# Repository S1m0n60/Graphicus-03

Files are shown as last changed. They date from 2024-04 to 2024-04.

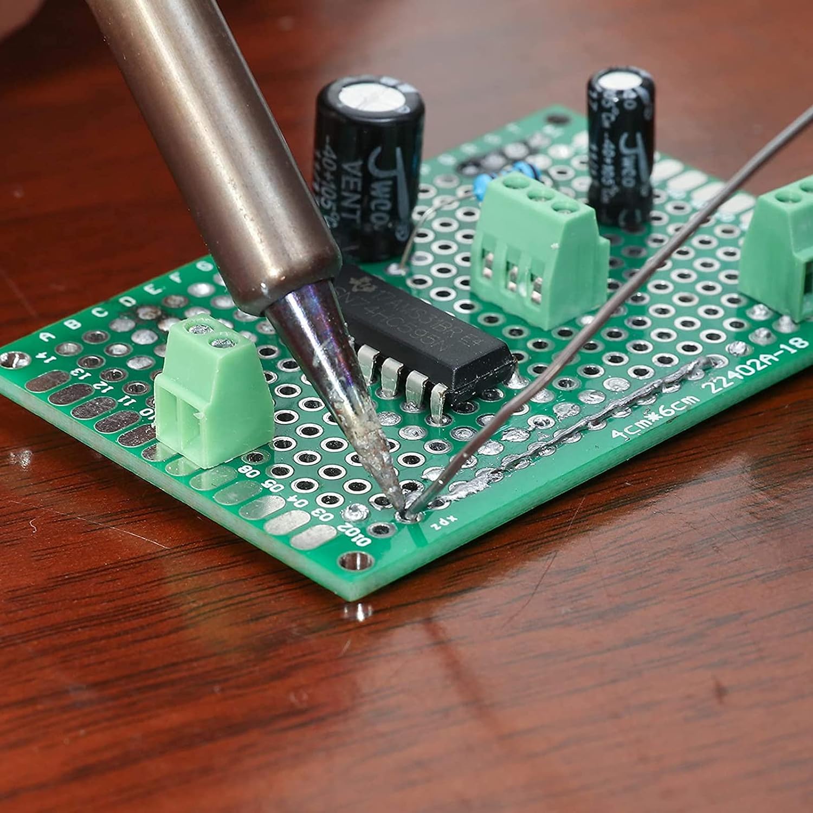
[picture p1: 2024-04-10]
Electrique/protoboard.jpg

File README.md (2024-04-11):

# **Graphicus-03**
## **Présentation**
<p style='text-align: justify;'> Graphicus-03 est une machine qui permet à l'opérateur de graver une image au choix sur un verre.
Ce repertoire permet à un utilisateur avec des connaissances de base en électronique, mécanique et informatique de fabriquer et mettre en marche un exemplaire de ce projet.
 
Pour plus d'informations, la documentation principale se trouve dans l' onglet [Wiki](https://github.com/S1m0n60/Graphicus-03/wiki) du projet.</p>

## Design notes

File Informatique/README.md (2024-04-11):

# **Section informatique**
<p style='text-align: justify;'>

Cette section contient toutes les ressources nécessaire pour faire l'intégration informatique de Graphicus-03.

Noter que les étapes à suivre pour effectuer l'assemblage se trouve dans le [Wiki](https://github.com/S1m0n60/Graphicus-03/wiki/Informatique).

</p>

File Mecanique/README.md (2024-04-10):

# **Section mécanique**
<p style='text-align: justify;'>

Cette section contient toutes les ressources nécessaire pour pouvoir assembler Graphicus-03.

Les ressources de cette section du répertoire sont divisé en deux section:

* [Les pièces à imprimer](https://github.com/S1m0n60/Graphicus-03/tree/main/Mecanique/Impression3D)
* [Les plan & devis](https://github.com/S1m0n60/Graphicus-03/tree/main/Mecanique/Plan%26Devis)

Noter que les étapes à suivre pour effectuer l'assemblage se trouve dans le [Wiki](https://github.com/S1m0n60/Graphicus-03/wiki/M%C3%A9canique).

</p>

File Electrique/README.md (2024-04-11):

# **Section électrique**
<p style='text-align: justify;'>

Cette section contient toutes les ressources nécessaire pour pouvoir réaliser les branchements de Graphicus-03.

## **Ressources importante**

* [Projet Autocad](https://github.com/S1m0n60/Graphicus-03/tree/main/Electrique/Team%20L%C3%A9vis%20et%20co)
* [Plan électrique en format PDF](https://github.com/S1m0n60/Graphicus-03/blob/main/Electrique/Team%20L%C3%A9vis%20et%20co.pdf)

Noter que les étapes à suivre pour effectuer l'assemblage se trouve dans le [Wiki](https://github.com/S1m0n60/Graphicus-03/wiki/%C3%89lectrique).

</p>

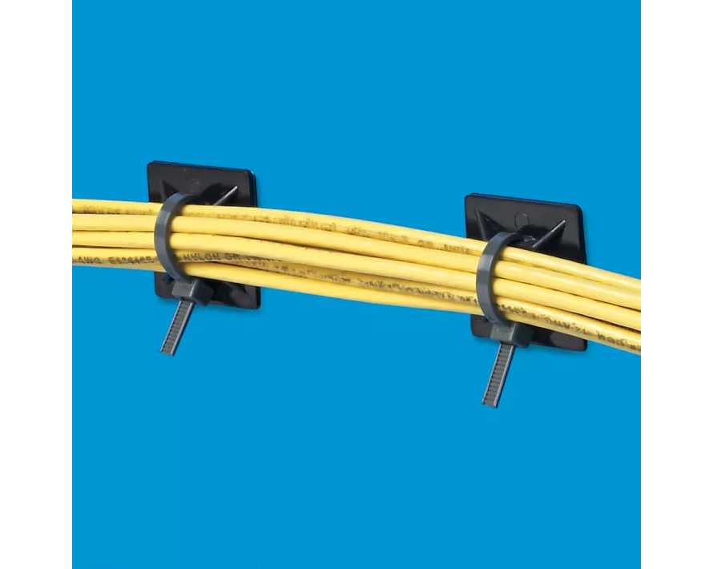
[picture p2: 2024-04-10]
Electrique/ZipTieCollant.png

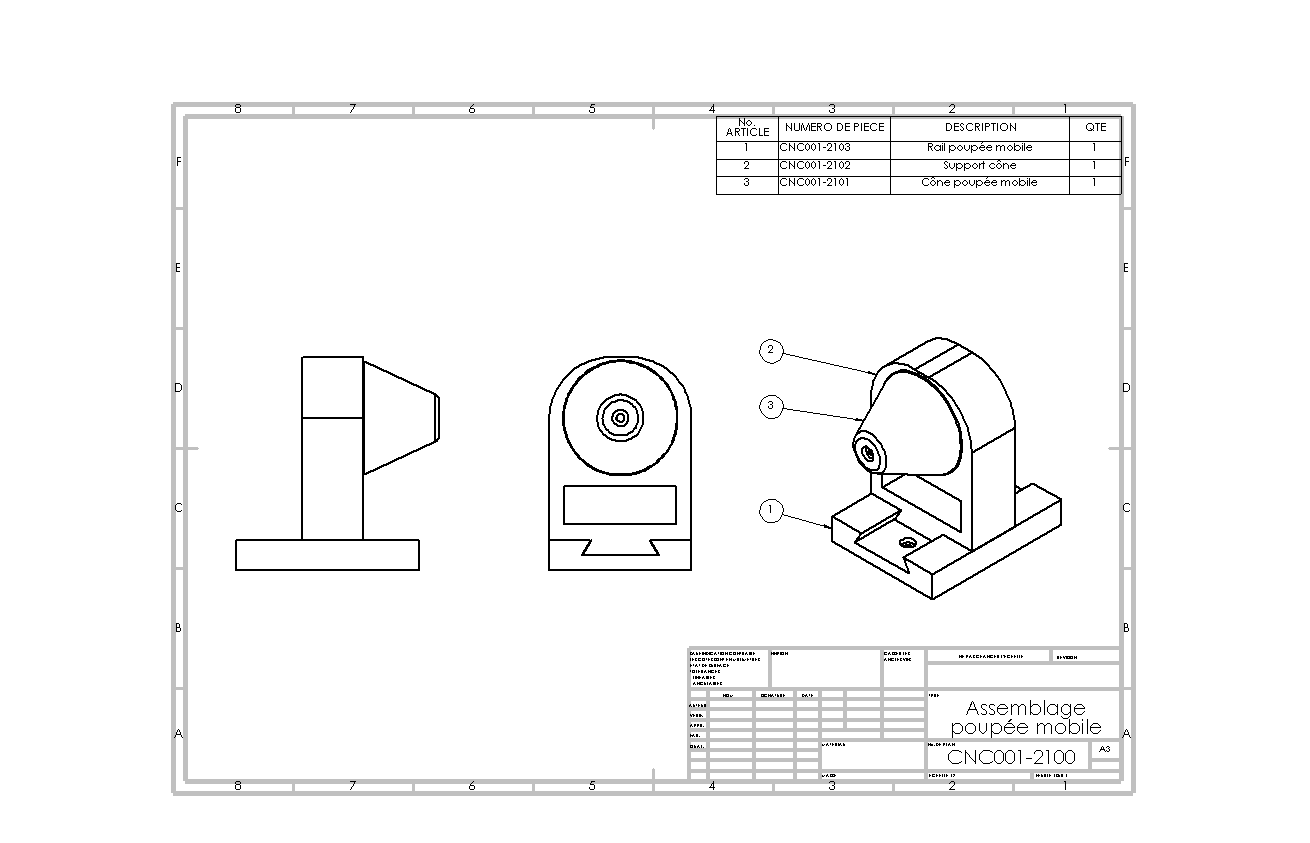
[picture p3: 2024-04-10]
Mecanique/Plan&Devis/Fichier_PNG/CNC001-2100.PNG

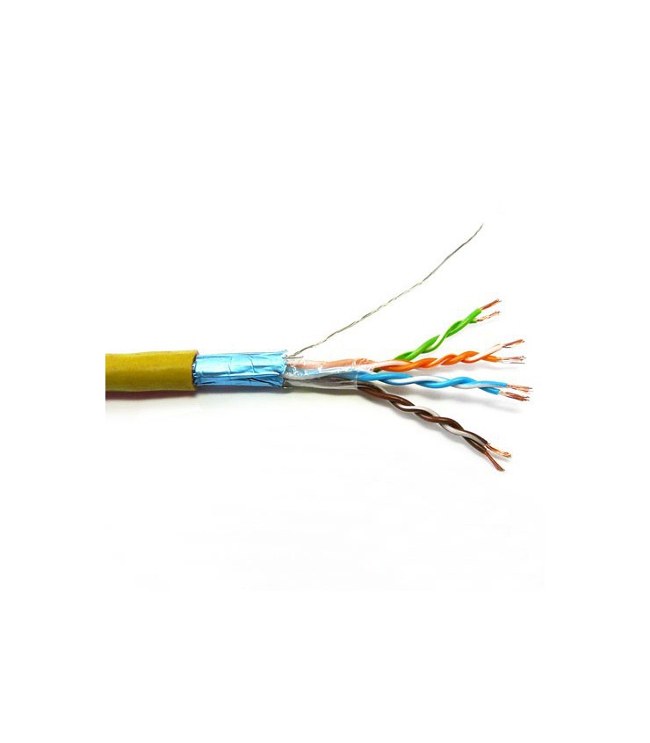
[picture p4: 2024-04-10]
Electrique/multibrin.jpg

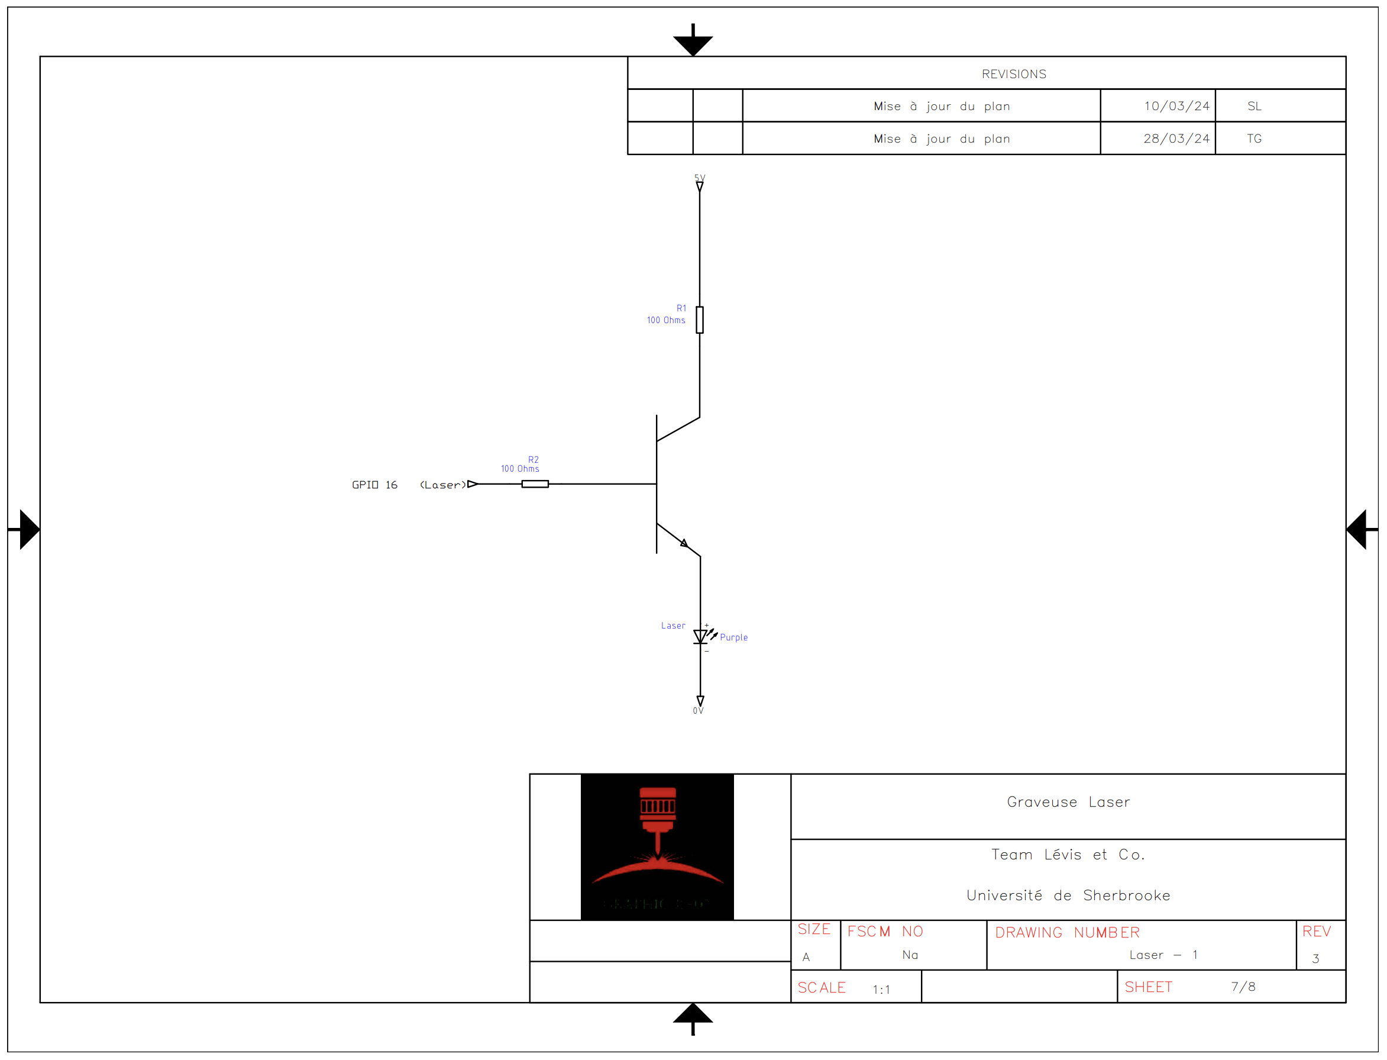
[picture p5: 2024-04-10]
Electrique/laser.PNG

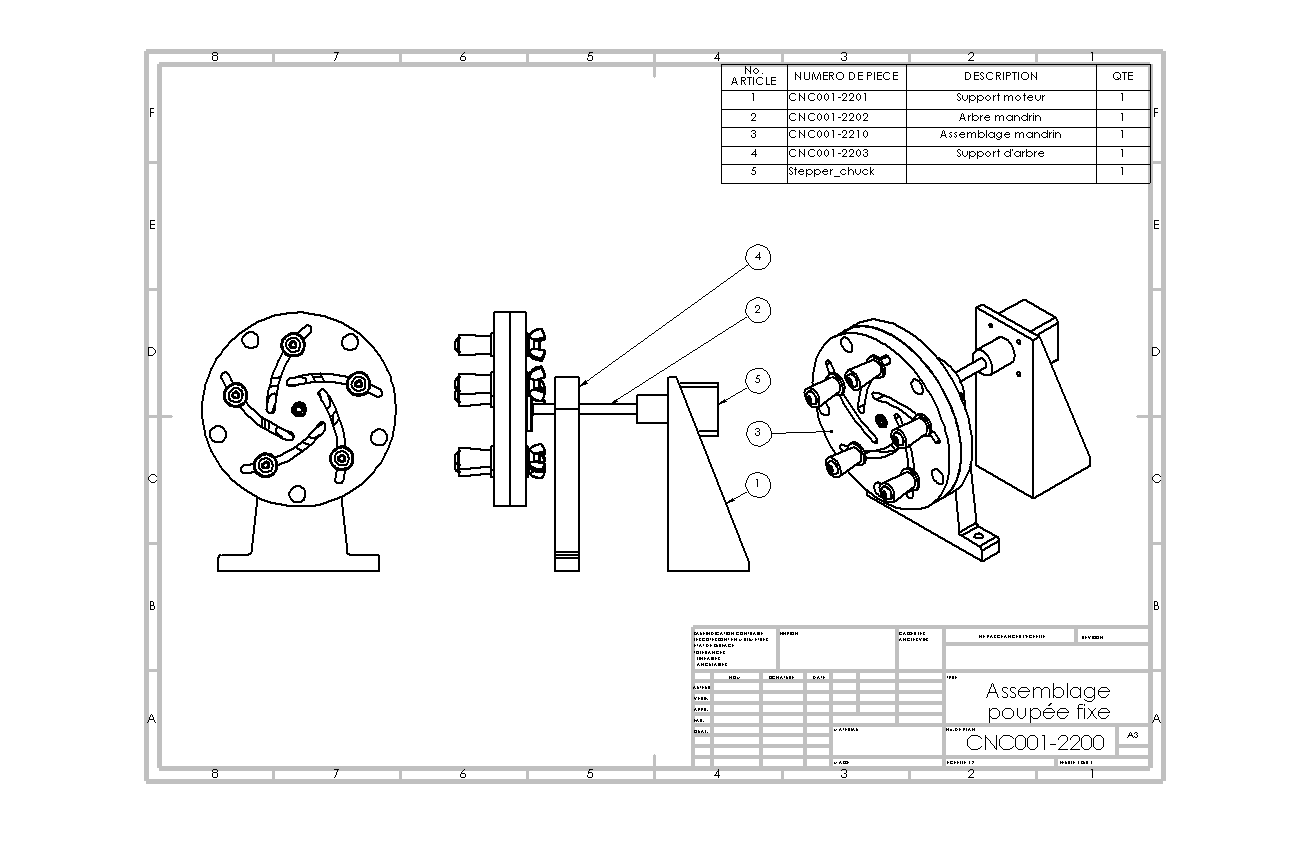
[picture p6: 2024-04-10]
Mecanique/Plan&Devis/Fichier_PNG/CNC001-2200.PNG

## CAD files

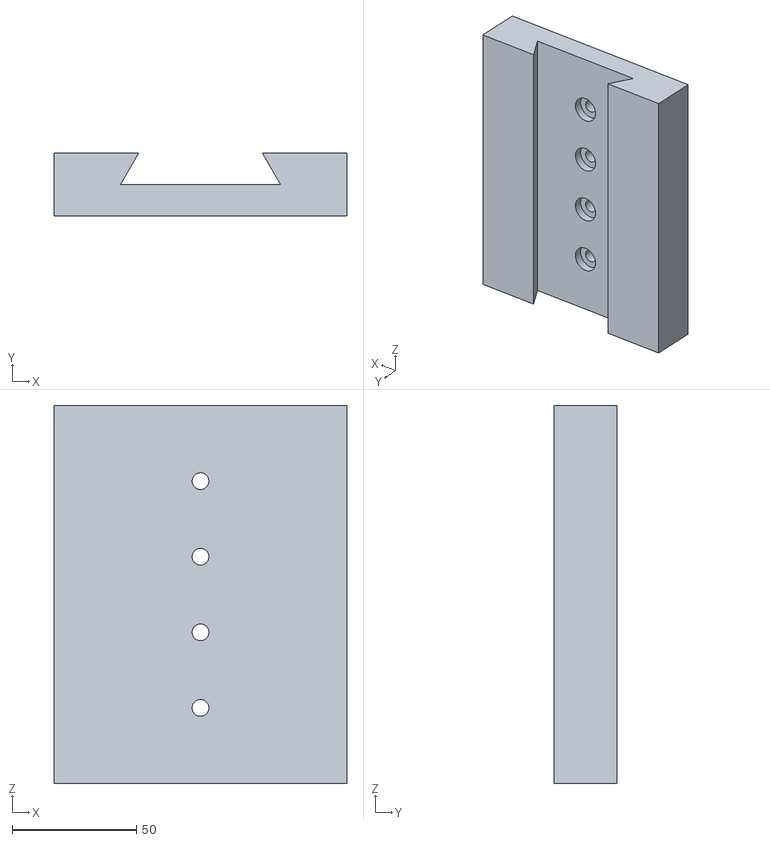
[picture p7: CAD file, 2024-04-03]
Mecanique/Impression3D/CNC001-2103.STL
118.1 x 25.4 x 152.4

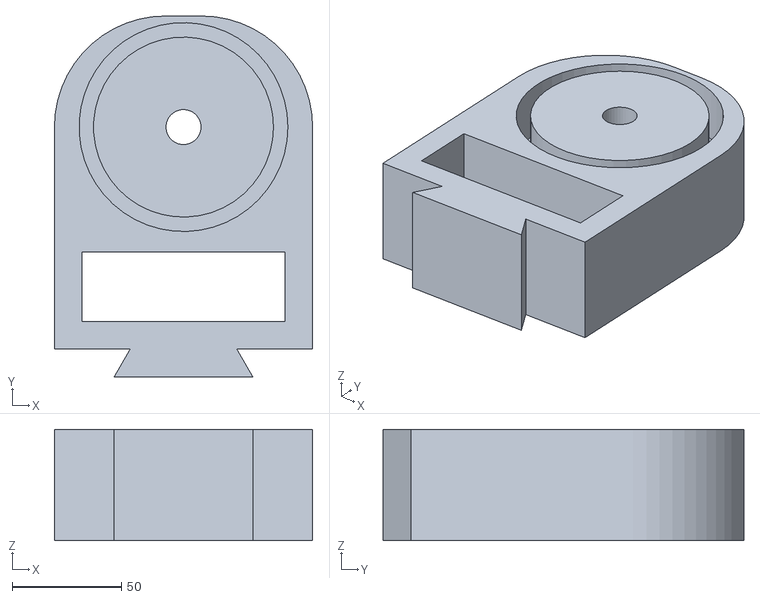
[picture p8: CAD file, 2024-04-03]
Mecanique/Impression3D/CNC001-2102.STL
118.1 x 165.1 x 50.8

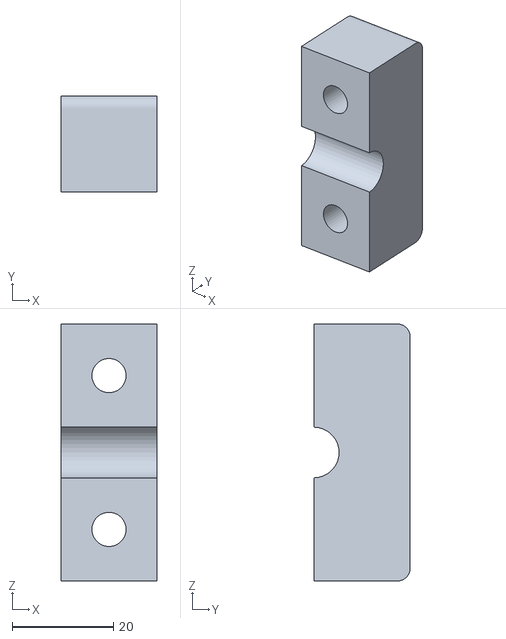
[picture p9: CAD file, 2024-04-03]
Mecanique/Impression3D/CNC001-2204.STL
19.1 x 19.1 x 50.8

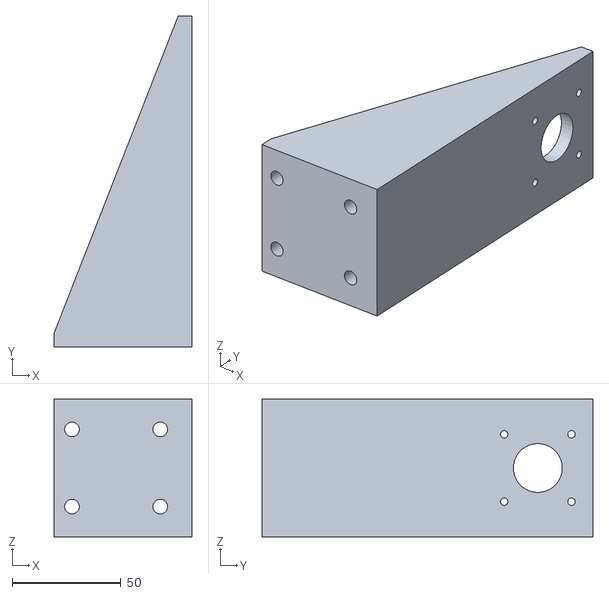
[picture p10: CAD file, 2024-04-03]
Mecanique/Impression3D/CNC001-2201.STL
63.5 x 152.4 x 63.5

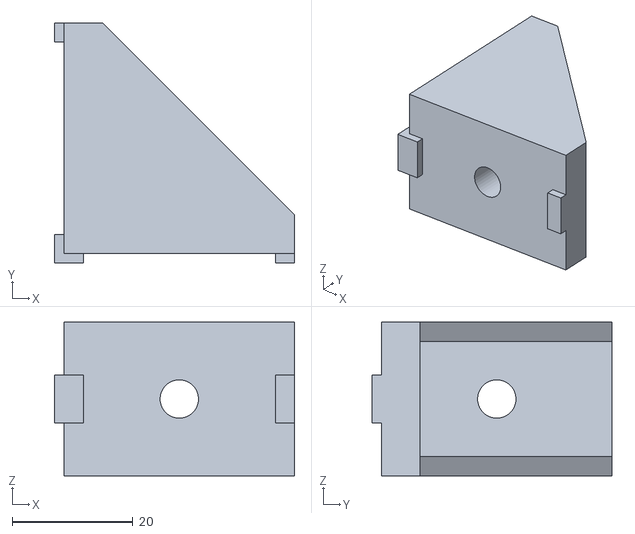
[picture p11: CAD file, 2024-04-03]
Mecanique/Impression3D/equerre.STL
39.7 x 39.7 x 25.4

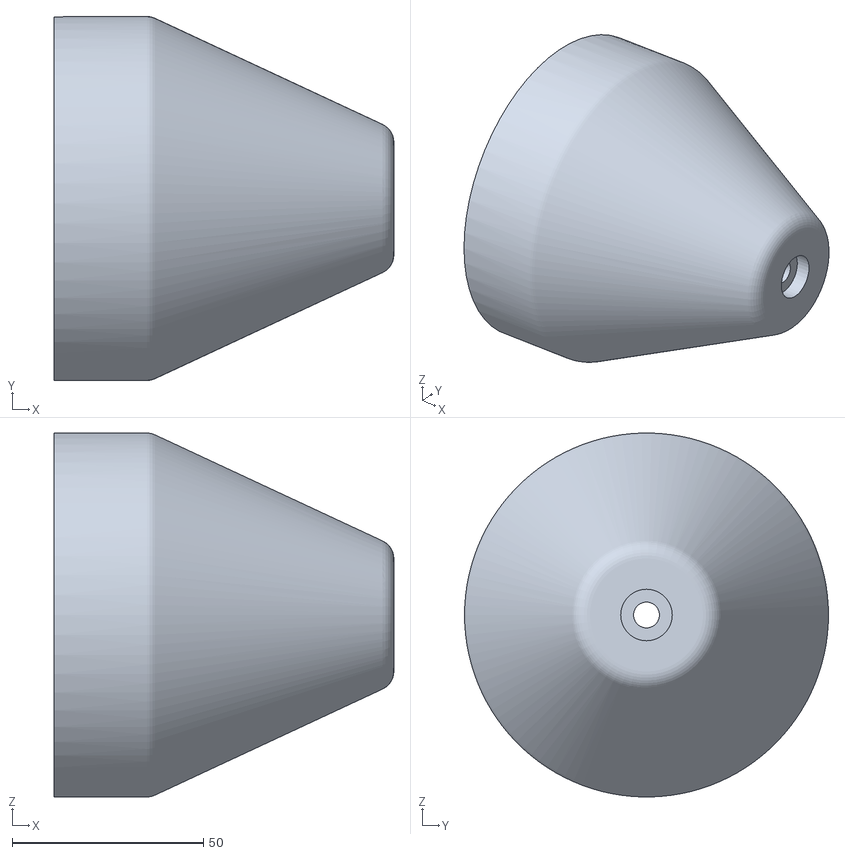
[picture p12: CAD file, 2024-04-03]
Mecanique/Impression3D/CNC001-2101.STL
88.9 x 95.2 x 95.2

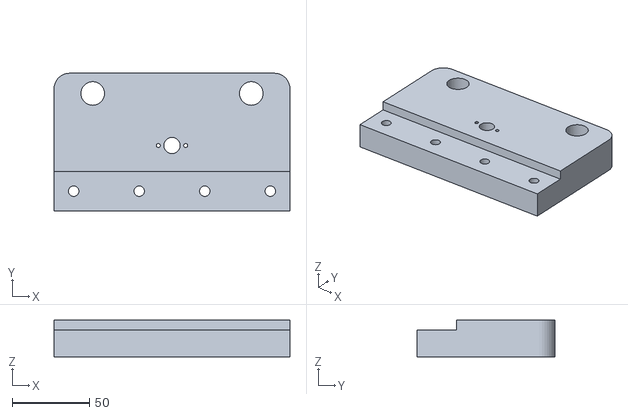
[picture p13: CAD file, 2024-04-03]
Mecanique/Impression3D/CNC001-2003.STL
152.4 x 88.9 x 23.8

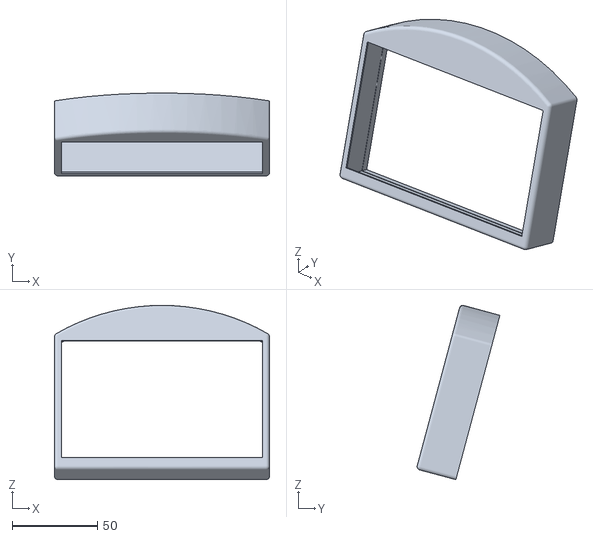
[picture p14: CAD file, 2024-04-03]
Mecanique/Impression3D/BoiteElectrique103.stl
126.0 x 48.5 x 102.1

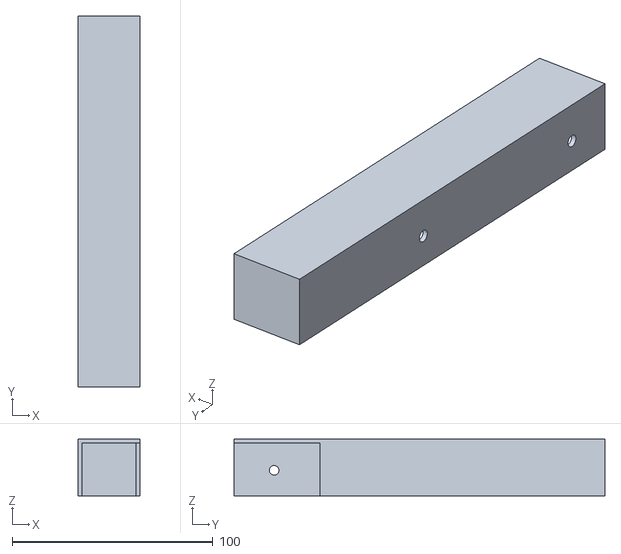
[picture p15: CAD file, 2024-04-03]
Mecanique/Impression3D/Support_ecran_gauche.stl
31.0 x 185.0 x 28.2

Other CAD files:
Electrique/Team Lévis et co/Low Voltage.dwg
Electrique/Team Lévis et co/Laser.dwg
Electrique/Team Lévis et co/LN298 (4).dwg
Electrique/Team Lévis et co/LN298 (1).dwg
Electrique/Team Lévis et co/LN298 (3).dwg
Electrique/Team Lévis et co/Raspberry Pi.dwg
Electrique/Team Lévis et co/Power.dwg
Electrique/Team Lévis et co/LN298 (2).dwg
Electrique/Team Lévis et co/Communication.dwg
Mecanique/Impression3D/BoiteElectrique100.stl
Mecanique/Impression3D/BoiteElectrique101.stl
Mecanique/Impression3D/CNC001-1002.STL
Mecanique/Impression3D/CNC001-1006.STL
Mecanique/Impression3D/CNC001-1007.STL
Mecanique/Impression3D/CNC001-2203.STL
Mecanique/Impression3D/CNC001-2303.STL
Mecanique/Impression3D/Support_ecran_avant.stl

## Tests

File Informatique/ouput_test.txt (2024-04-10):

1 1 1 1 1 1 1 1 1 1 1 1 1 1 1 1 1 1 1 1 1 1 1 1 1 1 1 1 1 1 1 1 1 1 1 1 1 1 1 1 1 1 1 1 1 1 1 1 1 1 1 1 1 1 1 1 1 1 1 1 1 1 1 1 1 1 1 1 1 1 1 1 1 1 1 1 1 1 1 1 1 1 1 1 1 1 1 1 1 1 1 1 1 1 1 1 1 1 1 1 1 1 1 1 1 1 1 1 1 1 1 1 1 1 1 1 1 1 1 1 1 1 1 1 1 1 1 1 1 1 1 1 1 1 1 1 1 1 
0 0 0 0 0 0 0 0 0 0 0 0 0 0 0 0 0 0 0 0 0 0 0 0 0 0 0 0 0 0 0 0 0 0 0 0 0 0 0 0 0 0 0 0 0 0 0 0 0 0 0 0 0 0 0 0 0 0 0 0 0 0 0 0 0 0 0 0 0 0 0 0 0 0 0 0 0 0 0 0 0 0 0 0 0 0 0 0 0 0 0 0 0 0 0 0 0 0 0 0 0 0 0 0 0 0 0 0 0 0 0 0 0 0 0 0 0 0 0 0 0 0 0 0 0 0 0 0 0 0 0 0 0 0 0 0 0 0 
0 0 0 0 0 0 0 0 0 0 0 0 0 0 0 0 0 0 0 0 0 0 0 0 0 0 0 0 0 0 0 0 0 0 0 0 0 0 0 0 0 0 0 0 0 0 0 0 0 0 0 0 0 0 0 0 0 0 0 0 0 0 0 0 0 0 0 0 0 0 0 0 0 0 0 0 0 0 0 0 0 0 0 0 0 0 0 0 0 0 0 0 0 0 0 0 0 0 0 0 0 0 0 0 0 0 0 0 0 0 0 0 0 0 0 0 0 0 0 0 0 0 0 0 0 0 0 0 0 0 0 0 0 0 0 0 0 0 
0 0 0 0 0 0 0 0 0 0 0 0 0 0 0 0 0 0 0 0 0 0 0 0 0 0 0 0 0 0 0 0 0 0 0 0 0 0 0 0 0 0 0 0 0 0 0 0 0 0 0 0 0 0 0 0 0 0 0 0 0 0 0 0 0 0 0 0 0 0 0 0 0 0 0 0 0 0 0 0 0 0 0 0 0 0 0 0 0 0 0 0 0 0 0 0 0 0 0 0 0 0 0 0 0 0 0 0 0 0 0 0 0 0 0 0 0 0 0 0 0 0 0 0 0 0 0 0 0 0 0 0 0 0 0 0 0 0 
0 0 0 0 0 0 0 0 0 0 0 0 0 0 0 0 0 0 0 0 0 0 0 0 0 0 0 0 0 0 0 0 0 0 0 0 0 0 0 0 0 0 0 0 0 0 0 0 0 0 0 0 0 0 0 0 0 0 0 0 0 0 0 0 0 0 0 0 0 0 0 0 0 0 0 0 0 0 0 0 0 0 0 0 0 0 0 0 0 0 0 0 0 0 0 0 0 0 0 0 0 0 0 0 0 0 0 0 0 0 0 0 0 0 0 0 0 0 0 0 0 0 0 0 0 0 0 0 0 0 0 0 0 0 0 0 0 0 
0 0 0 0 0 0 0 0 0 0 0 0 0 0 0 0 0 0 0 0 0 0 0 0 0 0 0 0 0 0 0 0 0 0 0 0 0 0 0 0 0 0 0 0 0 0 0 0 0 0 0 0 0 0 0 0 0 0 0 0 0 0 0 0 0 0 0 0 0 0 0 0 0 0 0 0 0 0 0 0 0 0 0 0 0 0 0 0 0 0 0 0 0 0 0 0 0 0 0 0 0 0 0 0 0 0 0 0 0 0 0 0 0 0 0 0 0 0 0 0 0 0 0 0 0 0 0 0 0 0 0 0 0 0 0 0 0 0 
0 0 0 0 0 0 0 0 0 0 0 0 0 0 0 0 0 0 0 0 0 0 0 0 0 0 0 0 0 0 0 0 0 0 0 0 0 0 0 0 0 0 0 0 0 0 0 0 0 0 0 0 0 0 0 0 0 0 0 0 0 0 0 0 0 0 0 0 0 0 0 0 0 0 0 0 0 0 0 0 0 0 0 0 0 0 0 0 0 0 0 0 0 0 0 0 0 0 0 0 0 0 0 0 0 0 0 0 0 0 0 0 0 0 0 0 0 0 0 0 0 0 0 0 0 0 0 0 0 0 0 0 0 0 0 0 0 0 
0 0 0 0 0 0 0 0 0 0 0 0 0 0 0 0 0 0 0 0 0 0 0 0 0 0 0 0 0 0 0 0 0 0 0 0 0 0 0 0 0 0 0 0 0 0 0 0 0 0 0 0 0 0 0 0 0 0 0 0 0 0 0 0 0 0 0 0 0 0 0 0 0 0 0 0 0 0 0 0 0 0 0 0 0 0 0 0 0 0 0 0 0 0 0 0 0 0 0 0 0 0 0 0 0 0 0 0 0 0 0 0 0 0 0 0 0 0 0 0 0 0 0 0 0 0 0 0 0 0 0 0 0 0 0 0 0 0 
0 0 0 0 0 0 0 0 0 0 0 0 0 0 0 0 0 0 0 0 0 0 0 0 0 0 0 0 0 0 0 0 0 0 0 0 0 0 0 0 0 0 0 0 0 0 0 0 0 0 0 0 0 0 0 0 0 0 0 0 0 0 0 0 0 0 0 0 0 0 0 0 0 0 0 0 0 0 0 0 0 0 0 0 0 0 0 0 0 0 0 0 0 0 0 0 0 0 0 0 0 0 0 0 0 0 0 0 0 0 0 0 0 0 0 0 0 0 0 0 0 0 0 0 0 0 0 0 0 0 0 0 0 0 0 0 0 0 
0 0 0 0 0 0 0 0 0 0 0 0 0 0 0 0 0 0 0 0 0 0 0 0 0 0 0 0 0 0 0 0 0 0 0 0 0 0 0 0 0 0 0 0 0 0 0 0 0 0 0 0 0 0 0 0 0 0 0 0 0 0 0 0 0 0 0 0 0 0 0 0 0 0 0 0 0 0 0 0 0 0 0 0 0 0 0 0 0 0 0 0 0 0 0 0 0 0 0 0 0 0 0 0 0 0 0 0 0 0 0 0 0 0 0 0 0 0 0 0 0 0 0 0 0 0 0 0 0 0 0 0 0 0 0 0 0 0 
0 0 0 0 0 0 0 0 0 0 0 0 0 0 0 0 0 0 0 0 0 0 0 0 0 0 0 0 0 0 0 0 0 0 0 0 0 0 0 0 0 0 0 0 0 0 0 0 0 0 0 0 0 0 0 0 0 0 0 0 0 0 0 0 0 0 0 0 0 0 0 0 0 0 0 0 0 0 0 0 0 0 0 0 0 0 0 0 0 0 0 0 0 0 0 0 0 0 0 0 0 0 0 0 0 0 0 0 0 0 0 0 0 0 0 0 0 0 0 0 0 0 0 0 0 0 0 0 0 0 0 0 0 0 0 0 0 0 
0 0 0 0 0 0 0 0 0 0 0 0 0 0 0 0 0 0 0 0 0 0 0 0 0 0 0 0 0 0 0 0 0 0 0 0 0 0 0 0 0 0 0 0 0 0 0 0 0 0 0 0 0 0 0 0 0 0 0 0 0 0 0 0 0 0 0 0 0 0 0 0 0 0 0 0 0 0 0 0 0 0 0 0 0 0 0 0 0 0 0 0 0 0 0 0 0 0 0 0 0 0 0 0 0 0 0 0 0 0 0 0 0 0 0 0 0 0 0 0 0 0 0 0 0 0 0 0 0 0 0 0 0 0 0 0 0 0 
0 0 0 0 0 0 0 0 0 0 0 0 0 0 0 0 0 0 0 0 0 0 0 0 0 0 0 0 0 0 0 0 0 0 0 0 0 0 0 0 0 0 0 0 0 0 0 0 0 0 0 0 0 0 0 0 0 0 0 0 0 0 0 0 0 0 0 0 0 0 0 0 0 0 0 0 0 0 0 0 0 0 0 0 0 0 0 0 0 0 0 0 0 0 0 0 0 0 0 0 0 0 0 0 0 0 0 0 0 0 0 0 0 0 0 0 0 0 0 0 0 0 0 0 0 0 0 0 0 0 0 0 0 0 0 0 0 0 
0 0 0 0 0 0 0 0 0 0 0 0 0 0 0 0 0 0 0 0 0 0 0 0 0 0 0 0 0 0 0 0 0 0 0 0 0 0 0 0 0 0 0 0 0 0 0 0 0 0 0 0 0 0 0 0 0 0 0 0 0 0 0 0 0 0 0 0 0 0 0 0 0 0 0 0 0 0 0 0 0 0 0 0 0 0 0 0 0 0 0 0 0 0 0 0 0 0 0 0 0 0 0 0 0 0 0 0 0 0 0 0 0 0 0 0 0 0 0 0 0 0 0 0 0 0 0 0 0 0 0 0 0 0 0 0 0 0 
0 0 0 0 0 0 0 0 0 0 0 0 0 0 0 0 0 0 0 0 0 0 0 0 0 0 0 0 0 0 0 0 0 0 0 0 0 0 0 0 0 0 0 0 0 0 0 0 0 0 0 0 0 0 0 0 0 0 0 0 0 0 0 0 0 0 0 0 0 0 0 0 0 0 0 0 0 0 0 0 0 0 0 0 0 0 0 0 0 0 0 0 0 0 0 0 0 0 0 0 0 0 0 0 0 0 0 0 0 0 0 0 0 0 0 0 0 0 0 0 0 0 0 0 0 0 0 0 0 0 0 0 0 0 0 0 0 0 
0 0 0 0 0 0 0 0 0 0 0 0 0 0 0 0 0 0 0 0 0 0 0 0 0 0 0 0 0 0 0 0 0 0 0 0 0 0 0 0 0 0 0 0 0 0 0 0 0 0 0 0 0 0 0 0 0 0 0 0 0 0 0 0 0 0 0 0 0 0 0 0 0 0 0 0 0 0 0 0 0 0 0 0 0 0 0 0 0 0 0 0 0 0 0 0 0 0 0 0 0 0 0 0 0 0 0 0 0 0 0 0 0 0 0 0 0 0 0 0 0 0 0 0 0 0 0 0 0 0 0 0 0 0 0 0 0 0 
0 0 0 0 0 0 0 0 0 0 0 0 0 0 0 0 0 0 0 0 0 0 0 0 0 0 0 0 0 0 0 0 0 0 0 0 0 0 0 0 0 0 0 0 0 0 0 0 0 0 0 0 0 0 0 0 0 0 0 0 0 0 0 0 0 0 0 0 0 0 0 0 0 0 0 0 0 0 0 0 0 0 0 0 0 0 0 0 0 0 0 0 0 0 0 0 0 0 0 0 0 0 0 0 0 0 0 0 0 0 0 0 0 0 0 0 0 0 0 0 0 0 0 0 0 0 0 0 0 0 0 0 0 0 0 0 0 0 
0 0 0 0 0 0 0 0 0 0 0 0 0 0 0 0 0 0 0 0 0 0 0 0 0 0 0 0 0 0 0 0 0 0 0 0 0 0 0 0 0 0 0 0 0 0 0 0 0 0 0 0 0 0 0 0 0 0 0 0 0 0 0 0 0 0 0 0 0 0 0 0 0 0 0 0 0 0 0 0 0 0 0 0 0 0 0 0 0 0 0 0 0 0 0 0 0 0 0 0 0 0 0 0 0 0 0 0 0 0 0 0 0 0 0 0 0 0 0 0 0 0 0 0 0 0 0 0 0 0 0 0 0 0 0 0 0 0 
0 0 0 0 0 0 0 0 0 0 0 0 0 0 0 0 0 0 0 0 0 0 0 0 0 0 0 0 0 0 0 0 0 0 0 0 0 0 0 0 0 0 0 0 0 0 0 0 0 0 0 0 0 0 0 0 0 0 0 0 0 0 0 0 0 0 0 0 0 0 0 0 0 0 0 0 0 0 0 0 0 0 0 0 0 0 0 0 0 0 0 0 0 0 0 0 0 0 0 0 0 0 0 0 0 0 0 0 0 0 0 0 0 0 0 0 0 0 0 0 0 0 0 0 0 0 0 0 0 0 0 0 0 0 0 0 0 0 
0 0 0 0 0 0 0 0 0 0 0 0 0 0 0 0 0 0 0 0 0 0 0 0 0 0 0 0 0 0 0 0 0 0 0 0 0 0 0 0 0 0 0 0 0 0 0 0 0 0 0 0 0 0 0 0 0 0 0 0 0 0 0 0 0 0 0 0 0 0 0 0 0 0 0 0 0 0 0 0 0 0 0 0 0 0 0 0 0 0 0 0 0 0 0 0 0 0 0 0 0 0 0 0 0 0 0 0 0 0 0 0 0 0 0 0 0 0 0 0 0 0 0 0 0 0 0 0 0 0 0 0 0 0 0 0 0 0 
0 0 0 0 0 0 0 0 0 0 0 0 0 0 0 0 0 0 0 0 0 0 0 0 0 0 0 0 0 0 0 0 0 0 0 0 0 0 0 0 0 0 0 0 0 0 0 0 0 0 0 0 0 0 0 0 0 0 0 0 0 0 0 0 0 0 0 0 0 0 0 0 0 0 0 0 0 0 0 0 0 0 0 0 0 0 0 0 0 0 0 0 0 0 0 0 0 0 0 0 0 0 0 0 0 0 0 0 0 0 0 0 0 0 0 0 0 0 0 0 0 0 0 0 0 0 0 0 0 0 0 0 0 0 0 0 0 0 
0 0 0 0 0 0 0 0 0 0 0 0 0 0 0 0 0 0 0 0 0 0 0 0 0 0 0 0 0 0 0 0 0 0 0 0 0 0 0 0 0 0 0 0 0 0 0 0 0 0 0 0 0 0 0 0 0 0 0 0 0 0 0 0 0 0 0 0 0 0 0 0 0 0 0 0 0 0 0 0 0 0 0 0 0 0 0 0 0 0 0 0 0 0 0 0 0 0 0 0 0 0 0 0 0 0 0 0 0 0 0 0 0 0 0 0 0 0 0 0 0 0 0 0 0 0 0 0 0 0 0 0 0 0 0 0 0 0 
0 0 0 0 0 0 0 0 0 0 0 0 0 0 0 0 0 0 0 0 0 0 0 0 0 0 0 0 0 0 0 0 0 0 0 0 0 0 0 0 0 0 0 0 0 0 0 0 0 0 0 0 0 0 0 0 0 0 0 0 0 0 0 0 0 0 0 0 0 0 0 0 0 0 0 0 0 0 0 0 0 0 0 0 0 0 0 0 0 0 0 0 0 0 0 0 0 0 0 0 0 0 0 0 0 0 0 0 0 0 0 0 0 0 0 0 0 0 0 0 0 0 0 0 0 0 0 0 0 0 0 0 0 0 0 0 0 0 
0 0 0 0 0 0 0 0 0 0 0 0 0 0 0 0 0 0 0 0 0 0 0 0 0 0 0 0 0 0 0 0 0 0 0 0 0 0 0 0 0 0 0 0 0 0 0 0 0 0 0 0 0 0 0 0 0 0 0 0 0 0 0 0 0 0 0 0 0 0 0 0 0 0 0 0 0 0 0 0 0 0 0 0 0 0 0 0 0 0 0 0 0 0 0 0 0 0 0 0 0 0 0 0 0 0 0 0 0 0 0 0 0 0 0 0 0 0 0 0 0 0 0 0 0 0 0 0 0 0 0 0 0 0 0 0 0 0 
0 0 0 0 0 0 0 0 0 0 0 0 0 0 0 0 0 0 0 0 0 0 0 0 0 0 0 0 0 0 0 0 0 0 0 0 0 0 0 0 0 0 0 0 0 0 0 0 0 0 0 0 0 0 0 0 0 0 0 0 0 0 0 0 0 0 0 0 0 0 0 0 0 0 0 0 0 0 0 0 0 0 0 0 0 0 0 0 0 0 0 0 0 0 0 0 0 0 0 0 0 0 0 0 0 0 0 0 0 0 0 0 0 0 0 0 0 0 0 0 0 0 0 0 0 0 0 0 0 0 0 0 0 0 0 0 0 0 
0 0 0 0 0 0 0 0 0 0 0 0 0 0 0 0 0 0 0 0 0 0 0 0 0 0 0 0 0 0 0 0 0 0 0 0 0 0 0 0 0 0 0 0 0 0 0 0 0 0 0 0 0 0 0 0 0 0 0 0 0 0 0 0 0 0 0 0 0 0 0 0 0 0 0 0 0 0 0 0 0 0 0 0 0 0 0 0 0 0 0 0 0 0 0 0 0 0 0 0 0 0 0 0 0 0 0 0 0 0 0 0 0 0 0 0 0 0 0 0 0 0 0 0 0 0 0 0 0 0 0 0 0 0 0 0 0 0 
0 0 0 0 0 0 0 0 0 0 0 0 0 0 0 0 0 0 0 0 0 0 0 0 0 0 0 0 0 0 0 0 0 0 0 0 0 0 0 0 0 0 0 0 0 0 0 0 0 0 0 0 0 0 0 0 0 0 0 0 0 0 0 0 0 0 0 0 0 0 0 0 0 0 0 0 0 0 0 0 0 0 0 0 0 0 0 0 0 0 0 0 0 0 0 0 0 0 0 0 0 0 0 0 0 0 0 0 0 0 0 0 0 0 0 0 0 0 0 0 0 0 0 0 0 0 0 0 0 0 0 0 0 0 0 0 0 0 
0 0 0 0 0 0 0 0 0 0 0 0 0 0 0 0 0 0 0 0 0 0 0 0 0 0 0 0 0 0 0 0 0 0 0 0 0 0 0 0 0 0 0 0 0 0 0 0 0 0 0 0 0 0 0 0 0 0 0 0 0 0 0 0 0 0 0 0 0 0 0 0 0 0 0 0 0 0 0 0 0 0 0 0 0 0 0 0 0 0 0 0 0 0 0 0 0 0 0 0 0 0 0 0 0 0 0 0 0 0 0 0 0 0 0 0 0 0 0 0 0 0 0 0 0 0 0 0 0 0 0 0 0 0 0 0 0 0 
0 0 0 0 0 0 0 0 0 0 0 0 0 0 0 0 0 0 0 0 0 0 0 0 0 0 0 0 0 0 0 0 0 0 0 0 0 0 0 0 0 0 0 0 0 0 0 0 0 0 0 0 0 0 0 0 0 0 0 0 0 0 0 0 0 0 0 0 0 0 0 0 0 0 0 0 0 0 0 0 0 0 0 0 0 0 0 0 0 0 0 0 0 0 0 0 0 0 0 0 0 0 0 0 0 0 0 0 0 0 0 0 0 0 0 0 0 0 0 0 0 0 0 0 0 0 0 0 0 0 0 0 0 0 0 0 0 0 
0 0 0 0 0 0 0 0 0 0 0 0 0 0 0 0 0 0 0 0 0 0 0 0 0 0 0 0 0 0 0 0 0 0 0 0 0 0 0 0 0 0 0 0 0 0 0 0 0 0 0 0 0 0 0 0 0 0 0 0 0 0 0 0 0 0 0 0 0 0 0 0 0 0 0 0 0 0 0 0 0 0 0 0 0 0 0 0 0 0 0 0 0 0 0 0 0 0 0 0 0 0 0 0 0 0 0 0 0 0 0 0 0 0 0 0 0 0 0 0 0 0 0 0 0 0 0 0 0 0 0 0 0 0 0 0 0 0 
0 0 0 0 0 0 0 0 0 0 0 0 0 0 0 0 0 0 0 0 0 0 0 0 0 0 0 0 0 0 0 0 0 0 0 0 0 0 0 0 0 0 0 0 0 0 0 0 0 0 0 0 0 0 0 0 0 0 0 0 0 0 0 0 0 0 0 0 0 0 0 0 0 0 0 0 0 0 0 0 0 0 0 0 0 0 0 0 0 0 0 0 0 0 0 0 0 0 0 0 0 0 0 0 0 0 0 0 0 0 0 0 0 0 0 0 0 0 0 0 0 0 0 0 0 0 0 0 0 0 0 0 0 0 0 0 0 0 
0 0 0 0 0 0 0 0 0 0 0 0 0 0 0 0 0 0 0 0 0 0 0 0 0 0 0 0 0 0 0 0 0 0 0 0 0 0 0 0 0 0 0 0 0 0 0 0 0 0 0 0 0 0 0 0 0 0 0 0 0 0 0 0 0 0 0 0 0 0 0 0 0 0 0 0 0 0 0 0 0 0 0 0 0 0 0 0 0 0 0 0 0 0 0 0 0 0 0 0 0 0 0 0 0 0 0 0 0 0 0 0 0 0 0 0 0 0 0 0 0 0 0 0 0 0 0 0 0 0 0 0 0 0 0 0 0 0 
0 0 0 0 0 0 0 0 0 0 0 0 0 0 0 0 0 0 0 0 0 0 0 0 0 0 0 0 0 0 0 0 0 0 0 0 0 0 0 0 0 0 0 0 0 0 0 0 0 0 0 0 0 0 0 0 0 0 0 0 0 0 0 0 0 0 0 0 0 0 0 0 0 0 0 0 0 0 0 0 0 0 0 0 0 0 0 0 0 0 0 0 0 0 0 0 0 0 0 0 0 0 0 0 0 0 0 0 0 0 0 0 0 0 0 0 0 0 0 0 0 0 0 0 0 0 0 0 0 0 0 0 0 0 0 0 0 0 
0 0 0 0 0 0 0 0 0 0 0 0 0 0 0 0 0 0 0 0 0 0 0 0 0 0 0 0 0 0 0 0 0 0 0 0 0 0 0 0 0 0 0 0 0 0 0 0 0 0 0 0 0 0 0 0 0 0 0 0 0 0 0 0 0 0 0 0 0 0 0 0 0 0 0 0 0 0 0 0 0 0 0 0 0 0 0 0 0 0 0 0 0 0 0 0 0 0 0 0 0 0 0 0 0 0 0 0 0 0 0 0 0 0 0 0 0 0 0 0 0 0 0 0 0 0 0 0 0 0 0 0 0 0 0 0 0 0 
0 0 0 0 0 0 0 0 0 0 0 0 0 0 0 0 0 0 0 0 0 0 0 0 0 0 0 0 0 0 0 0 0 0 0 0 0 0 0 0 0 0 0 0 0 0 0 0 0 0 0 0 0 0 0 0 0 0 0 0 0 0 0 0 0 0 0 0 0 0 0 0 0 0 0 0 0 0 0 0 0 0 0 0 0 0 0 0 0 0 0 0 0 0 0 0 0 0 0 0 0 0 0 0 0 0 0 0 0 0 0 0 0 0 0 0 0 0 0 0 0 0 0 0 0 0 0 0 0 0 0 0 0 0 0 0 0 0 
0 0 0 0 0 0 0 0 0 0 0 0 0 0 0 0 0 0 0 0 0 0 0 0 0 0 0 0 0 0 0 0 0 0 0 0 0 0 0 0 0 0 0 0 0 0 0 0 0 0 0 0 0 0 0 0 0 0 0 0 0 0 0 0 0 0 0 0 0 0 0 0 0 0 0 0 0 0 0 0 0 0 0 0 0 0 0 0 0 0 0 0 0 0 0 0 0 0 0 0 0 0 0 0 0 0 0 0 0 0 0 0 0 0 0 0 0 0 0 0 0 0 0 0 0 0 0 0 0 0 0 0 0 0 0 0 0 0 
0 0 0 0 0 0 0 0 0 0 0 0 0 0 0 0 0 0 0 0 0 0 0 0 0 0 0 0 0 0 0 0 0 0 0 0 0 0 0 0 0 0 0 0 0 0 0 0 0 0 0 0 0 0 0 0 0 0 0 0 0 0 0 0 0 0 0 0 0 0 0 0 0 0 0 0 0 0 0 0 0 0 0 0 0 0 0 0 0 0 0 0 0 0 0 0 0 0 0 0 0 0 0 0 0 0 0 0 0 0 0 0 0 0 0 0 0 0 0 0 0 0 0 0 0 0 0 0 0 0 0 0 0 0 0 0 0 0 
0 0 0 0 0 0 0 0 0 0 0 0 0 0 0 0 0 0 0 0 0 0 0 0 0 0 0 0 0 0 0 0 0 0 0 0 0 0 0 0 0 0 0 0 0 0 0 0 0 0 0 0 0 0 0 0 0 0 0 0 0 0 0 0 0 0 0 0 0 0 0 0 0 0 0 0 0 0 0 0 0 0 0 0 0 0 0 0 0 0 0 0 0 0 0 0 0 0 0 0 0 0 0 0 0 0 0 0 0 0 0 0 0 0 0 0 0 0 0 0 0 0 0 0 0 0 0 0 0 0 0 0 0 0 0 0 0 0 
0 0 0 0 0 0 0 0 0 0 0 0 0 0 0 0 0 0 0 0 0 0 0 0 0 0 0 0 0 0 0 0 0 0 0 0 0 0 0 0 0 0 0 0 0 0 0 0 0 0 0 0 0 0 0 0 0 0 0 0 0 0 0 0 0 0 0 0 0 0 0 0 0 0 0 0 0 0 0 0 0 0 0 0 0 0 0 0 0 0 0 0 0 0 0 0 0 0 0 0 0 0 0 0 0 0 0 0 0 0 0 0 0 0 0 0 0 0 0 0 0 0 0 0 0 0 0 0 0 0 0 0 0 0 0 0 0 0 
0 0 0 0 0 0 0 0 0 0 0 0 0 0 0 0 0 0 0 0 0 0 0 0 0 0 0 0 0 0 0 0 0 0 0 0 0 0 0 0 0 0 0 0 0 0 0 0 0 0 0 0 0 0 0 0 0 0 0 0 0 0 0 0 0 0 0 0 0 0 0 0 0 0 0 0 0 0 0 0 0 0 0 0 0 0 0 0 0 0 0 0 0 0 0 0 0 0 0 0 0 0 0 0 0 0 0 0 0 0 0 0 0 0 0 0 0 0 0 0 0 0 0 0 0 0 0 0 0 0 0 0 0 0 0 0 0 0 
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

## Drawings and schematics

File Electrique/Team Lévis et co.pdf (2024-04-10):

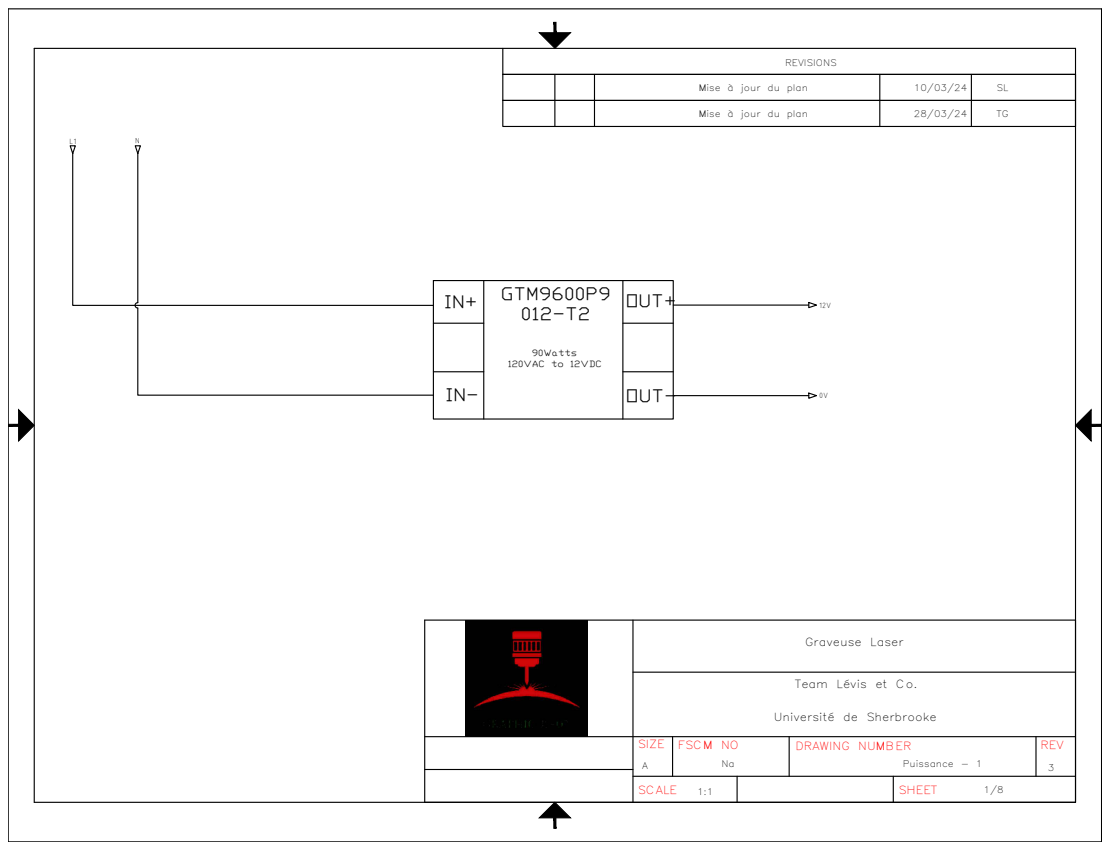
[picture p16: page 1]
REVISIONS Mise à jour du plan; SL SCALE; SHEET SIZE; FSCM NO; DRAWING NUMBER; REV Graveuse Laser Team Lévis et Co. Université de Sherbrooke A; Puissance - 1; 1/8 GTM9600P9 012-T2 IN+; OUT+ OUT- 90Watts 120VAC to 12VDC IN- L1; 12V 0V Mise à jour du plan

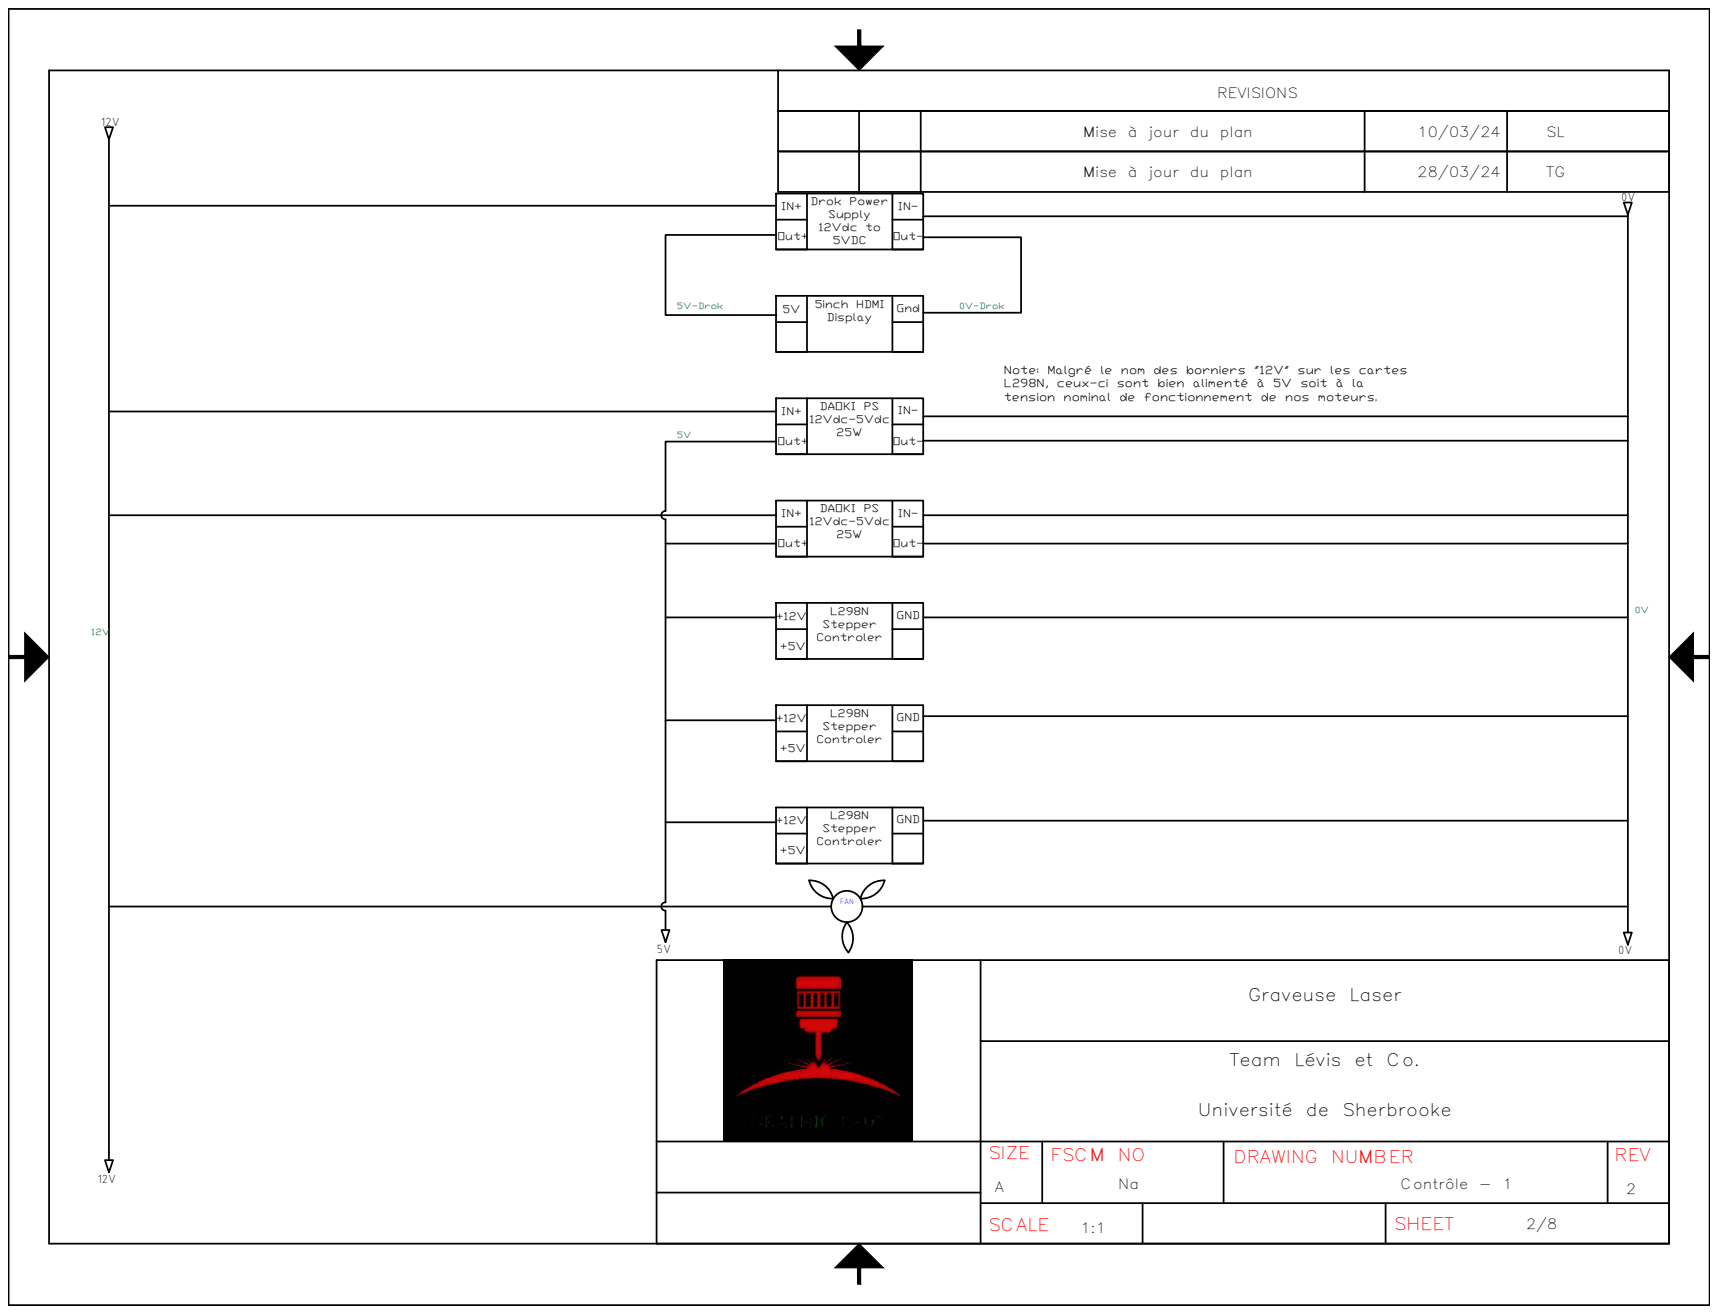
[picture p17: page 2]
REVISIONS Mise à jour du plan; SL SCALE; SHEET SIZE; FSCM NO; DRAWING NUMBER; REV Graveuse Laser Team Lévis et Co. Université de Sherbrooke A; Contrôle - 1; 2/8 Drok Power Supply 12Vdc to 5VDC IN+; IN- Out+; Out- 5inch HDMI Display 5V; Gnd DAOKI PS 12Vdc-5Vdc 25W IN+; Out- DAOKI PS 12Vdc-5Vdc 25W IN+; Out- L298N Stepper Controler +12V; GND +5V; L298N Stepper Controler +12V; GND +5V 12V 12V; 0V0V FAN 5V 5V-Drok; 0V-Drok 5V 12V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

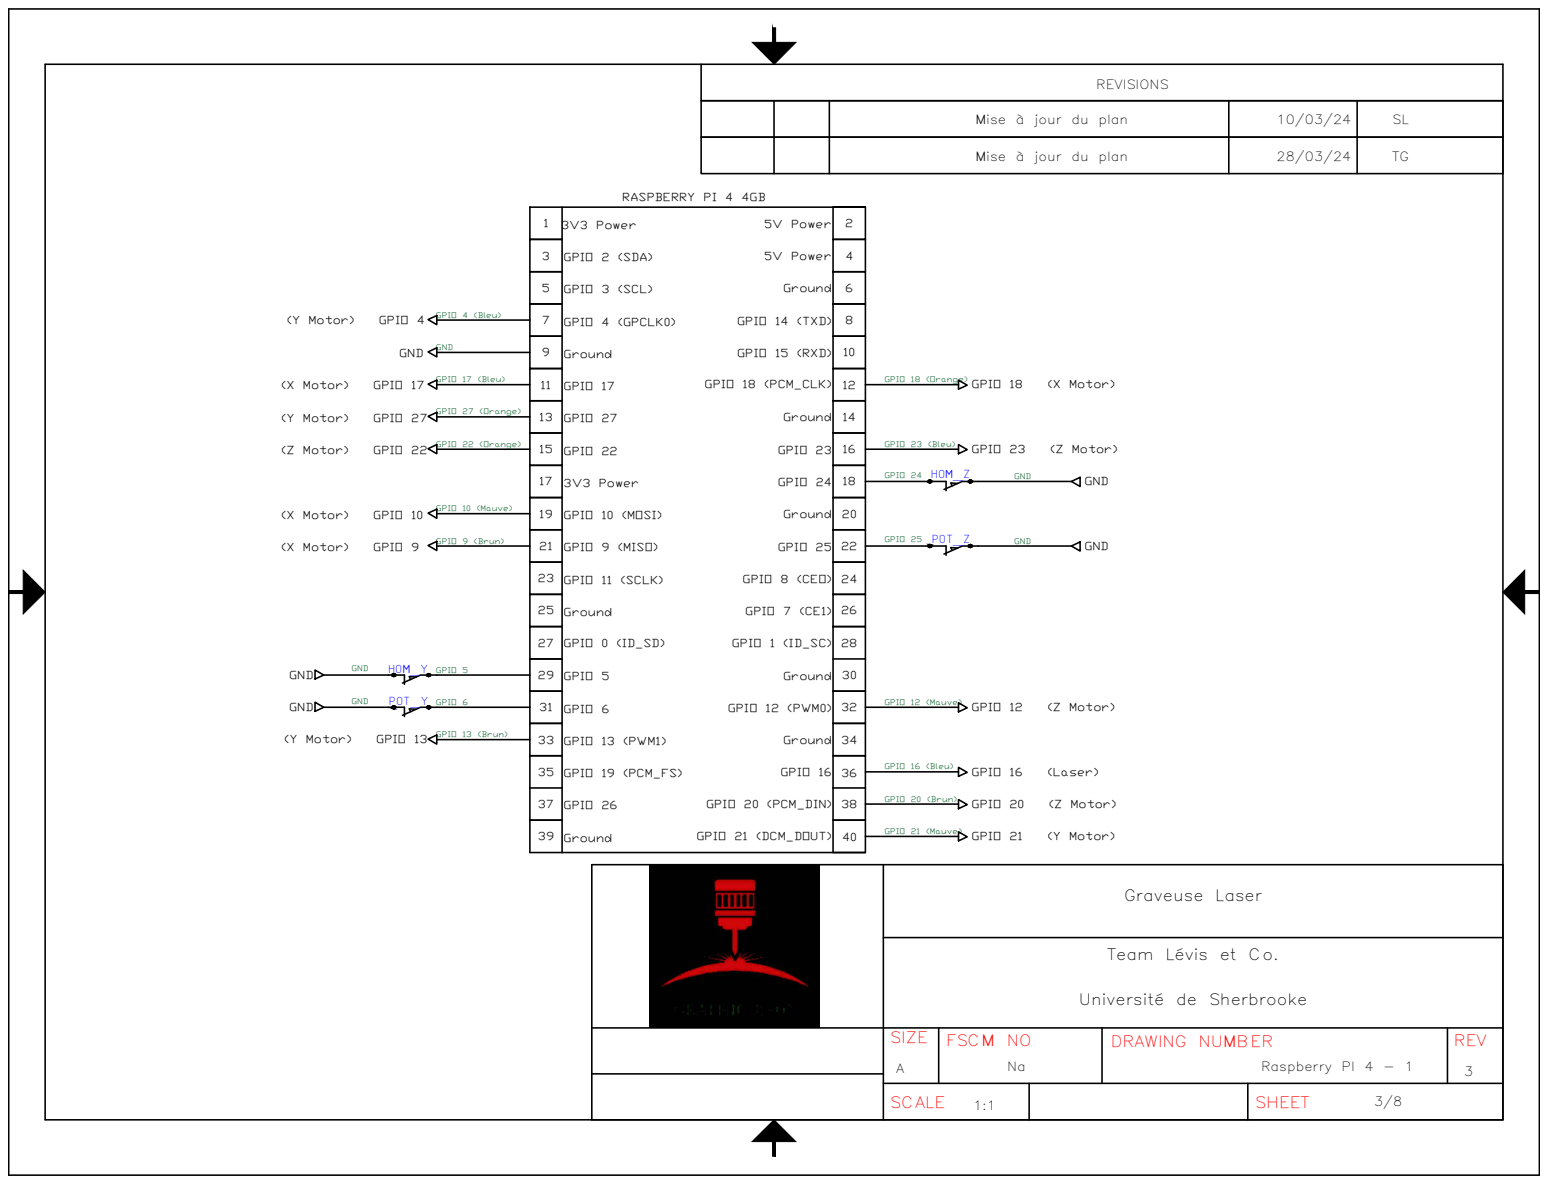
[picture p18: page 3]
REVISIONS Mise à jour du plan; SL SCALE; SHEET SIZE; FSCM NO; DRAWING NUMBER; REV Graveuse Laser Team Lévis et Co. Université de Sherbrooke A; Raspberry PI 4 - 1; 30 3234 RASPBERRY PI 4 4GB 3V3 Power GPIO 2 (SDA) 3739; 383640 GPIO 3 (SCL) GPIO 4 (GPCLK0) Ground GPIO 17 GPIO 27 GPIO 22 3V3 Power GPIO 10 (MOSI) GPIO 9 (MISO) GPIO 11 (SCLK) Ground GPIO 0 (ID_SD) GPIO 5 GPIO 6 GPIO 13 (PWM1) GPIO 19 (PCM_FS) GPIO 26 Ground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

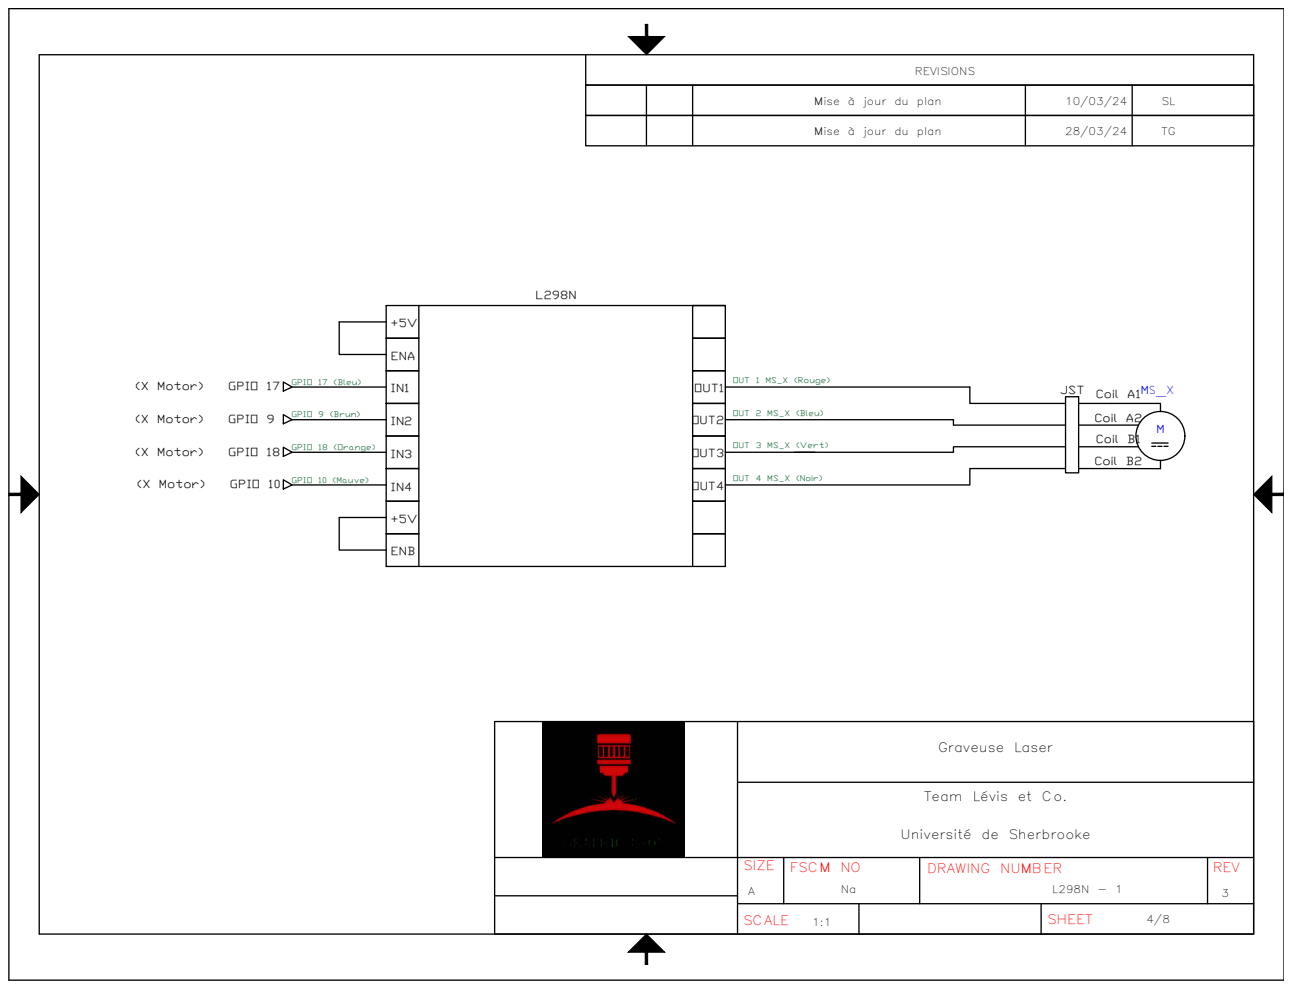
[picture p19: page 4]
REVISIONS Mise à jour du plan; SL SCALE; SHEET SIZE; FSCM NO; DRAWING NUMBER; REV Graveuse Laser Team Lévis et Co. Université de Sherbrooke A; 4/8 L298N ENA IN1 IN2 IN3 IN4; OUT1 OUT2 OUT3 OUT4 GPIO 9 (Brun) (X Motor); GPIO 9; OUT 4 MS_X (Noir) +5V ENB +5V GPIO 17 (Bleu) (X Motor); GPIO 17 GPIO 18 (Orange) (X Motor); GPIO 18 GPIO 10 (Mauve) (X Motor); GPIO 10; M MS_X Coil A1 Coil A2 Coil B2 JST Coil B1 OUT 3 MS_X (Vert) OUT 2 MS_X (Bleu) OUT 1 MS_X (Rouge) Mise à jour du plan

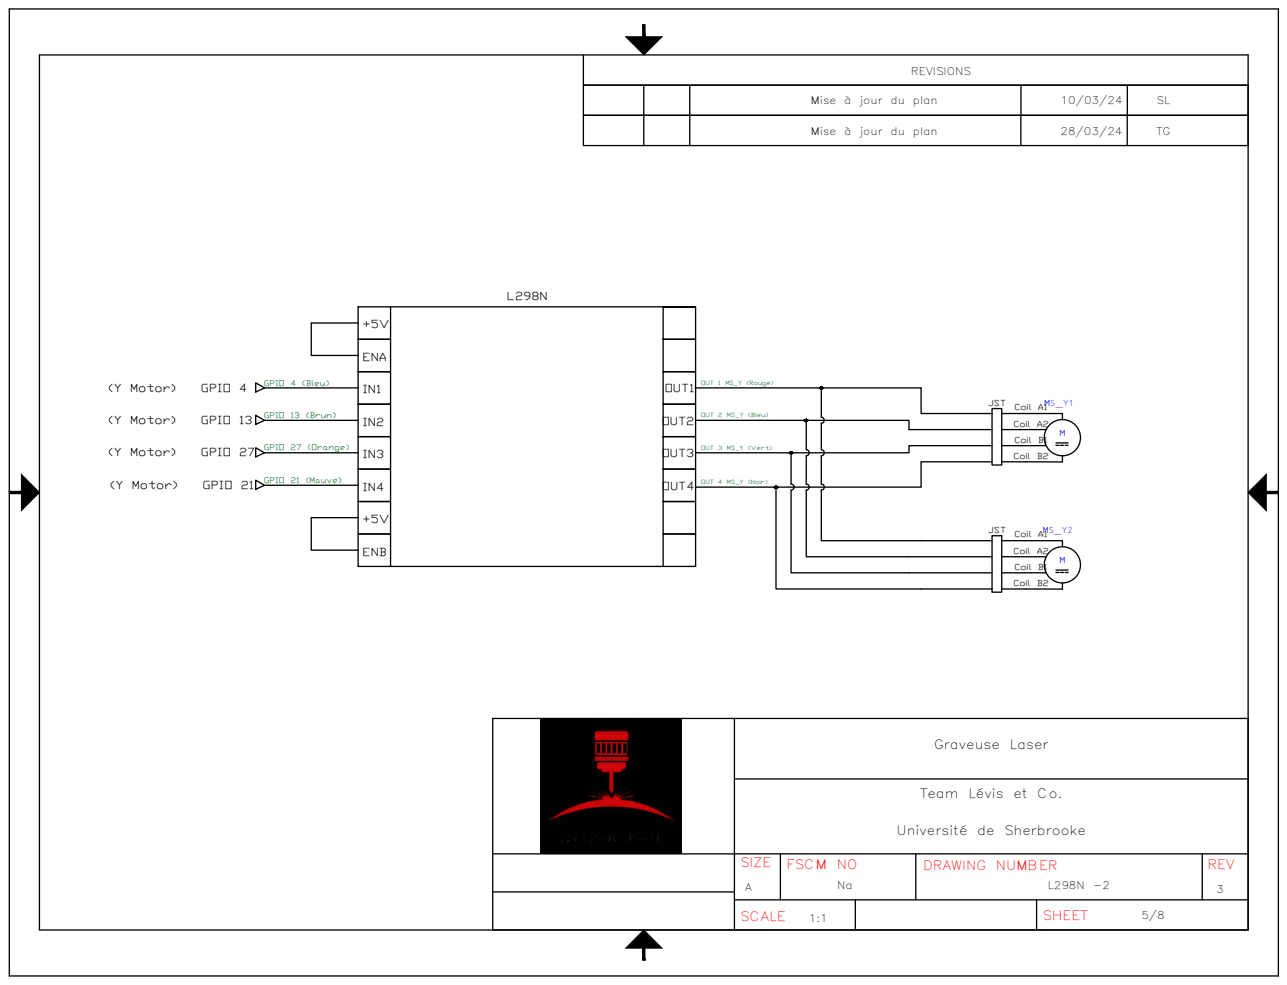
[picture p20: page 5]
REVISIONS OUT 4 MS_Y (Noir); M MS_Y1 Coil A1 Coil A2 Coil B2 JST Coil B1 OUT 3 MS_Y (Vert) OUT 2 MS_Y (Bleu) OUT 1 MS_Y (Rouge); M MS_Y2 Coil A1 Coil A2 Coil B2 JST Coil B1 SCALE; SHEET SIZE; FSCM NO; DRAWING NUMBER; REV Graveuse Laser Team Lévis et Co. Université de Sherbrooke A; 5/8 L298N ENA IN1 IN2 IN3 IN4; OUT1 OUT2 OUT3 OUT4 GPIO 13 (Brun) (Y Motor); GPIO 13; +5V ENB +5V GPIO 4 (Bleu) (Y Motor); GPIO 4; GPIO 27 (Orange) (Y Motor); GPIO 27 GPIO 21 (Mauve) (Y Motor); GPIO 21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

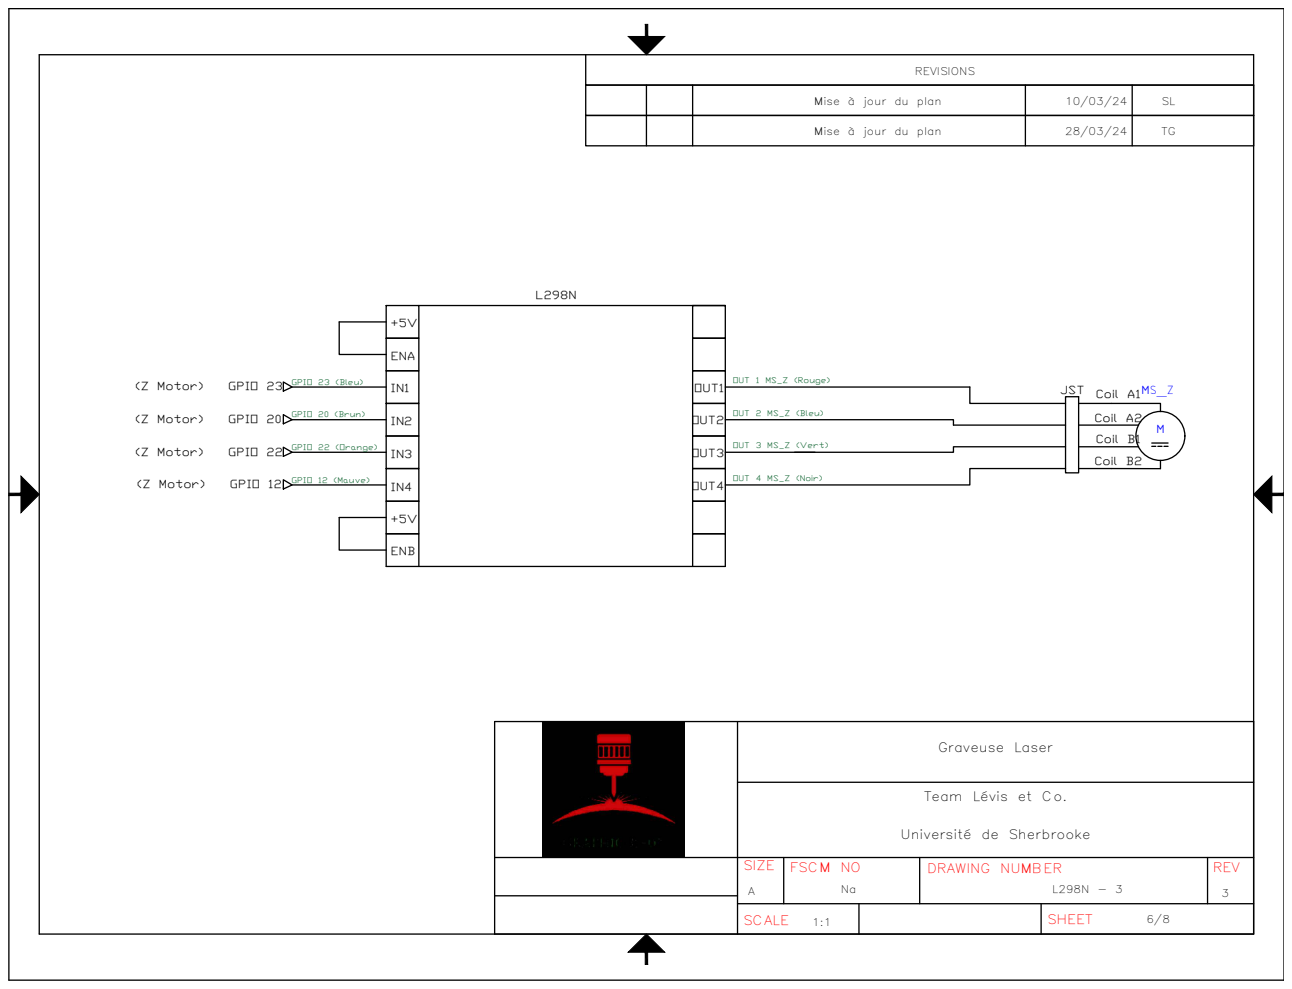
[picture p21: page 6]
REVISIONS Mise à jour du plan; SL SCALE; SHEET SIZE; FSCM NO; DRAWING NUMBER; REV Graveuse Laser Team Lévis et Co. Université de Sherbrooke A; 6/8 L298N ENA IN1 IN2 IN3 IN4; OUT1 OUT2 OUT3 OUT4 GPIO 20 (Brun) (Z Motor); GPIO 20; OUT 4 MS_Z (Noir) +5V ENB +5V GPIO 23 (Bleu) (Z Motor); GPIO 23 GPIO 22 (Orange) (Z Motor); GPIO 22 GPIO 12 (Mauve) (Z Motor); GPIO 12; M MS_Z Coil A1 Coil A2 Coil B2 JST Coil B1 OUT 3 MS_Z (Vert) OUT 2 MS_Z (Bleu) OUT 1 MS_Z (Rouge) Mise à jour du plan

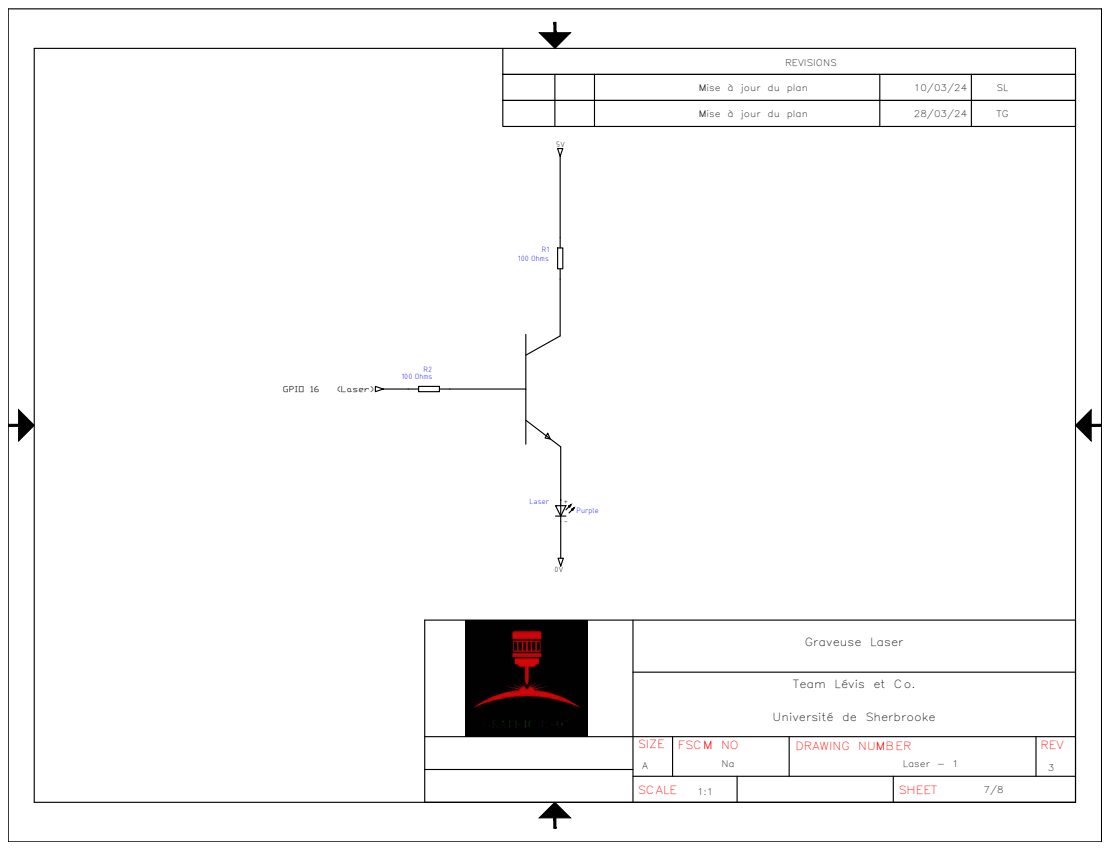
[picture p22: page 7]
REVISIONS Mise à jour du plan; SL SCALE; SHEET SIZE; FSCM NO; DRAWING NUMBER; REV Graveuse Laser Team Lévis et Co. Université de Sherbrooke A; Laser - 1; 7/8 100 OhmsR1 100 Ohms R2; 5V+- Purple Laser 0V GPIO 16; (Laser); Mise à jour du plan

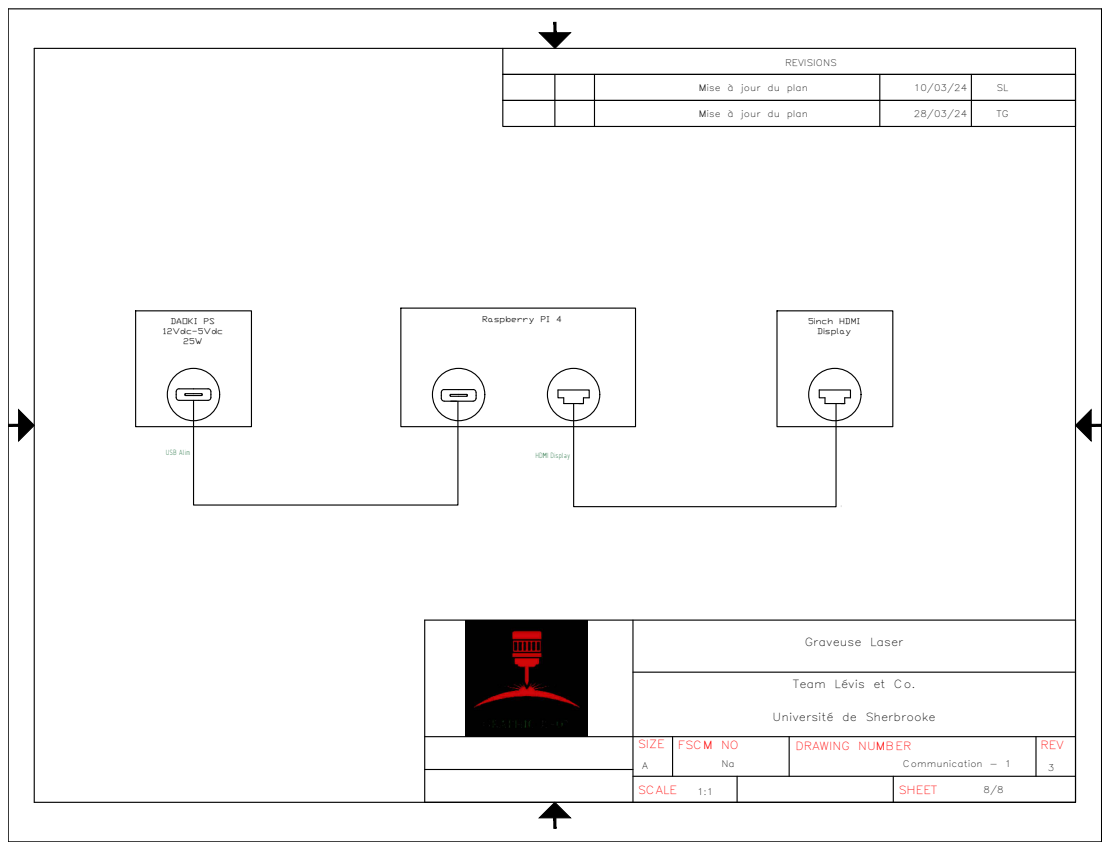
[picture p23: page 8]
REVISIONS Mise à jour du plan; SL SCALE; SHEET SIZE; FSCM NO; DRAWING NUMBER; REV Graveuse Laser Team Lévis et Co. Université de Sherbrooke A; Communication - 1; 8/8 5inch HDMI Display DAOKI PS; Raspberry PI 4 12Vdc-5Vdc 25W USB Alim; HDMI Display; Mise à jour du plan

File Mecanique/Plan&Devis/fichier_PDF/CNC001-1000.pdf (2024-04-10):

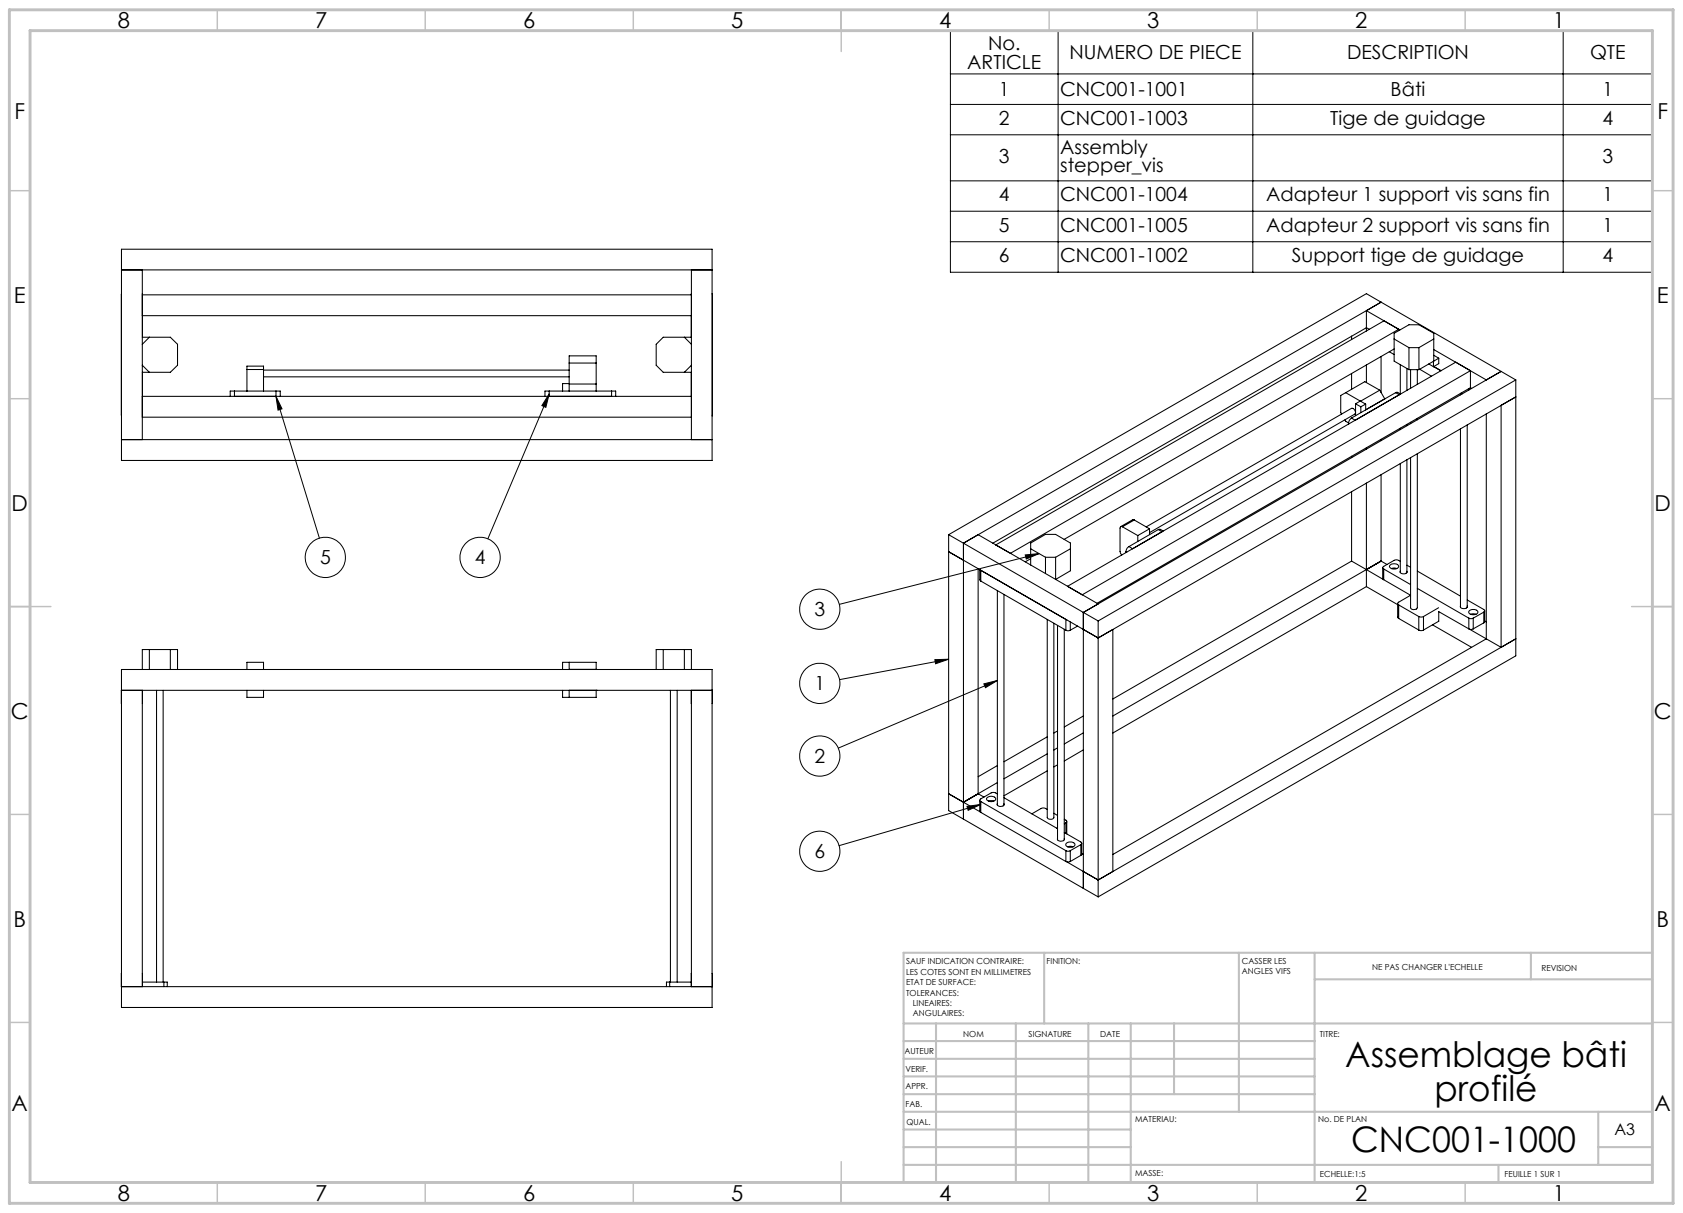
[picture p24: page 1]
FINITION:; CASSER LES; ANGLES VIFS; NE PAS CHANGER L'ECHELLE; REVISION; ECHELLE:1:5; FEUILLE 1 SUR 1

No. ARTICLE | NUMERO DE PIECE | DESCRIPTION | QTE
1 | CNC001-1001 | Bâti | 1
2 | CNC001-1003 | Tige de guidage | 4
3 | Assembly stepper_vis | | 3
4 | CNC001-1004 | Adapteur 1 support vis sans fin | 1
5 | CNC001-1005 | Adapteur 2 support vis sans fin | 1
6 | CNC001-1002 | Support tige de guidage | 4

SAUF INDICATION CONTRAIRE:
LES COTES SONT EN MILLIMETRES
ETAT DE SURFACE:
TOLERANCES:
LINEAIRES:
ANGULAIRES:

NOM | SIGNATURE | DATE | | | | TITRE: Assemblage bâti profilé

AUTEUR
VERIF.
APPR.
FAB.
QUAL. | | | | MATERIAU: | No. DE PLAN CNC001-1000 | A3

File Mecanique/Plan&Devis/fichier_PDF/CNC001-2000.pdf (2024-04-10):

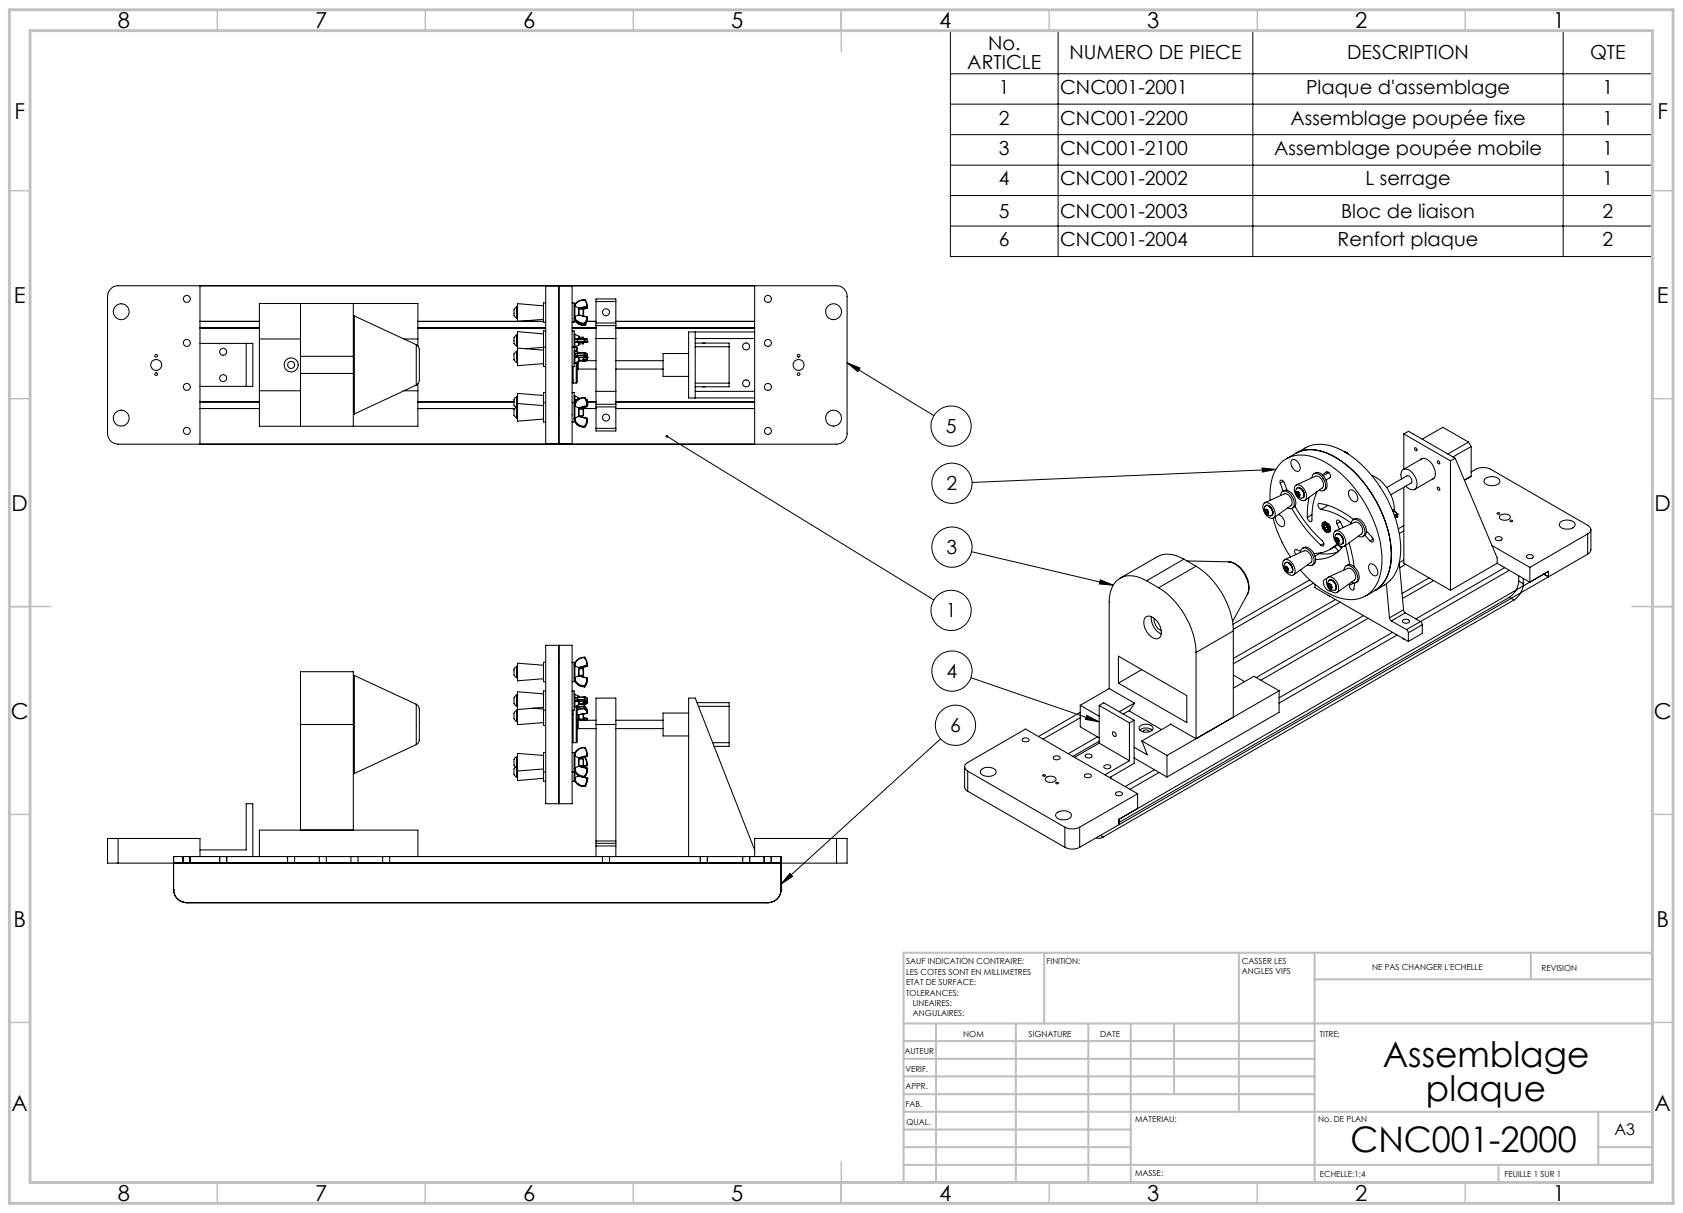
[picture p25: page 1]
FINITION:; CASSER LES; ANGLES VIFS; NE PAS CHANGER L'ECHELLE; REVISION; ECHELLE:1:4; FEUILLE 1 SUR 1

No. ARTICLE | NUMERO DE PIECE | DESCRIPTION | QTE
1 | CNC001-2001 | Plaque d'assemblage | 1
2 | CNC001-2200 | Assemblage poupée fixe | 1
3 | CNC001-2100 | Assemblage poupée mobile | 1
4 | CNC001-2002 | L serrage | 1
5 | CNC001-2003 | Bloc de liaison | 2
6 | CNC001-2004 | Renfort plaque | 2

SAUF INDICATION CONTRAIRE:
LES COTES SONT EN MILLIMETRES
ETAT DE SURFACE:
TOLERANCES:
LINEAIRES:
ANGULAIRES:

NOM | SIGNATURE | DATE | | | | TITRE: Assemblage plaque

AUTEUR
VERIF.
APPR.
FAB.
QUAL. | | | | MATERIAU: | No. DE PLAN CNC001-2000 | A3

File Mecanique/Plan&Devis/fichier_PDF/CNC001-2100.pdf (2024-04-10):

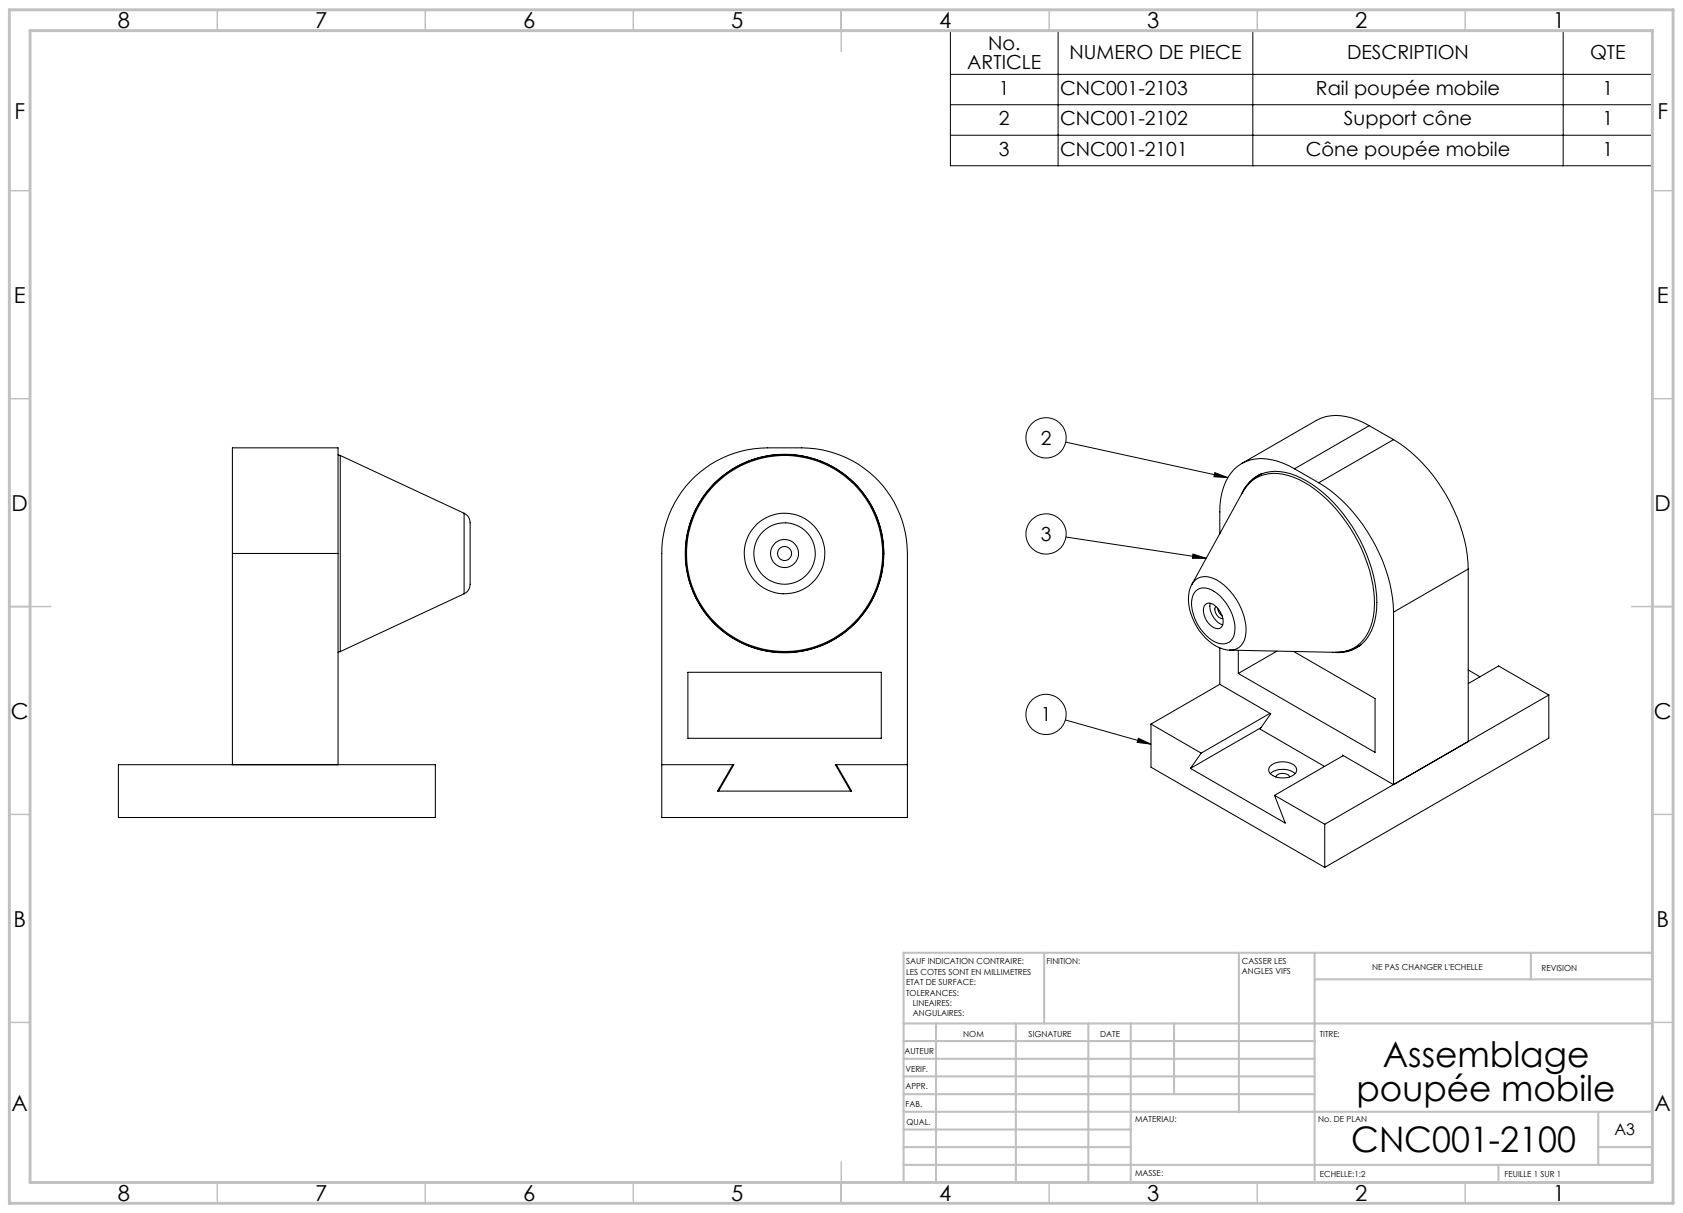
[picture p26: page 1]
FINITION:; CASSER LES; ANGLES VIFS; NE PAS CHANGER L'ECHELLE; REVISION; ECHELLE:1:2; FEUILLE 1 SUR 1

No. ARTICLE | NUMERO DE PIECE | DESCRIPTION | QTE
1 | CNC001-2103 | Rail poupée mobile | 1
2 | CNC001-2102 | Support cône | 1
3 | CNC001-2101 | Cône poupée mobile | 1

SAUF INDICATION CONTRAIRE:
LES COTES SONT EN MILLIMETRES
ETAT DE SURFACE:
TOLERANCES:
LINEAIRES:
ANGULAIRES:

NOM | SIGNATURE | DATE | | | | TITRE: Assemblage poupée mobile

AUTEUR
VERIF.
APPR.
FAB.
QUAL. | | | | MATERIAU: | No. DE PLAN CNC001-2100 | A3

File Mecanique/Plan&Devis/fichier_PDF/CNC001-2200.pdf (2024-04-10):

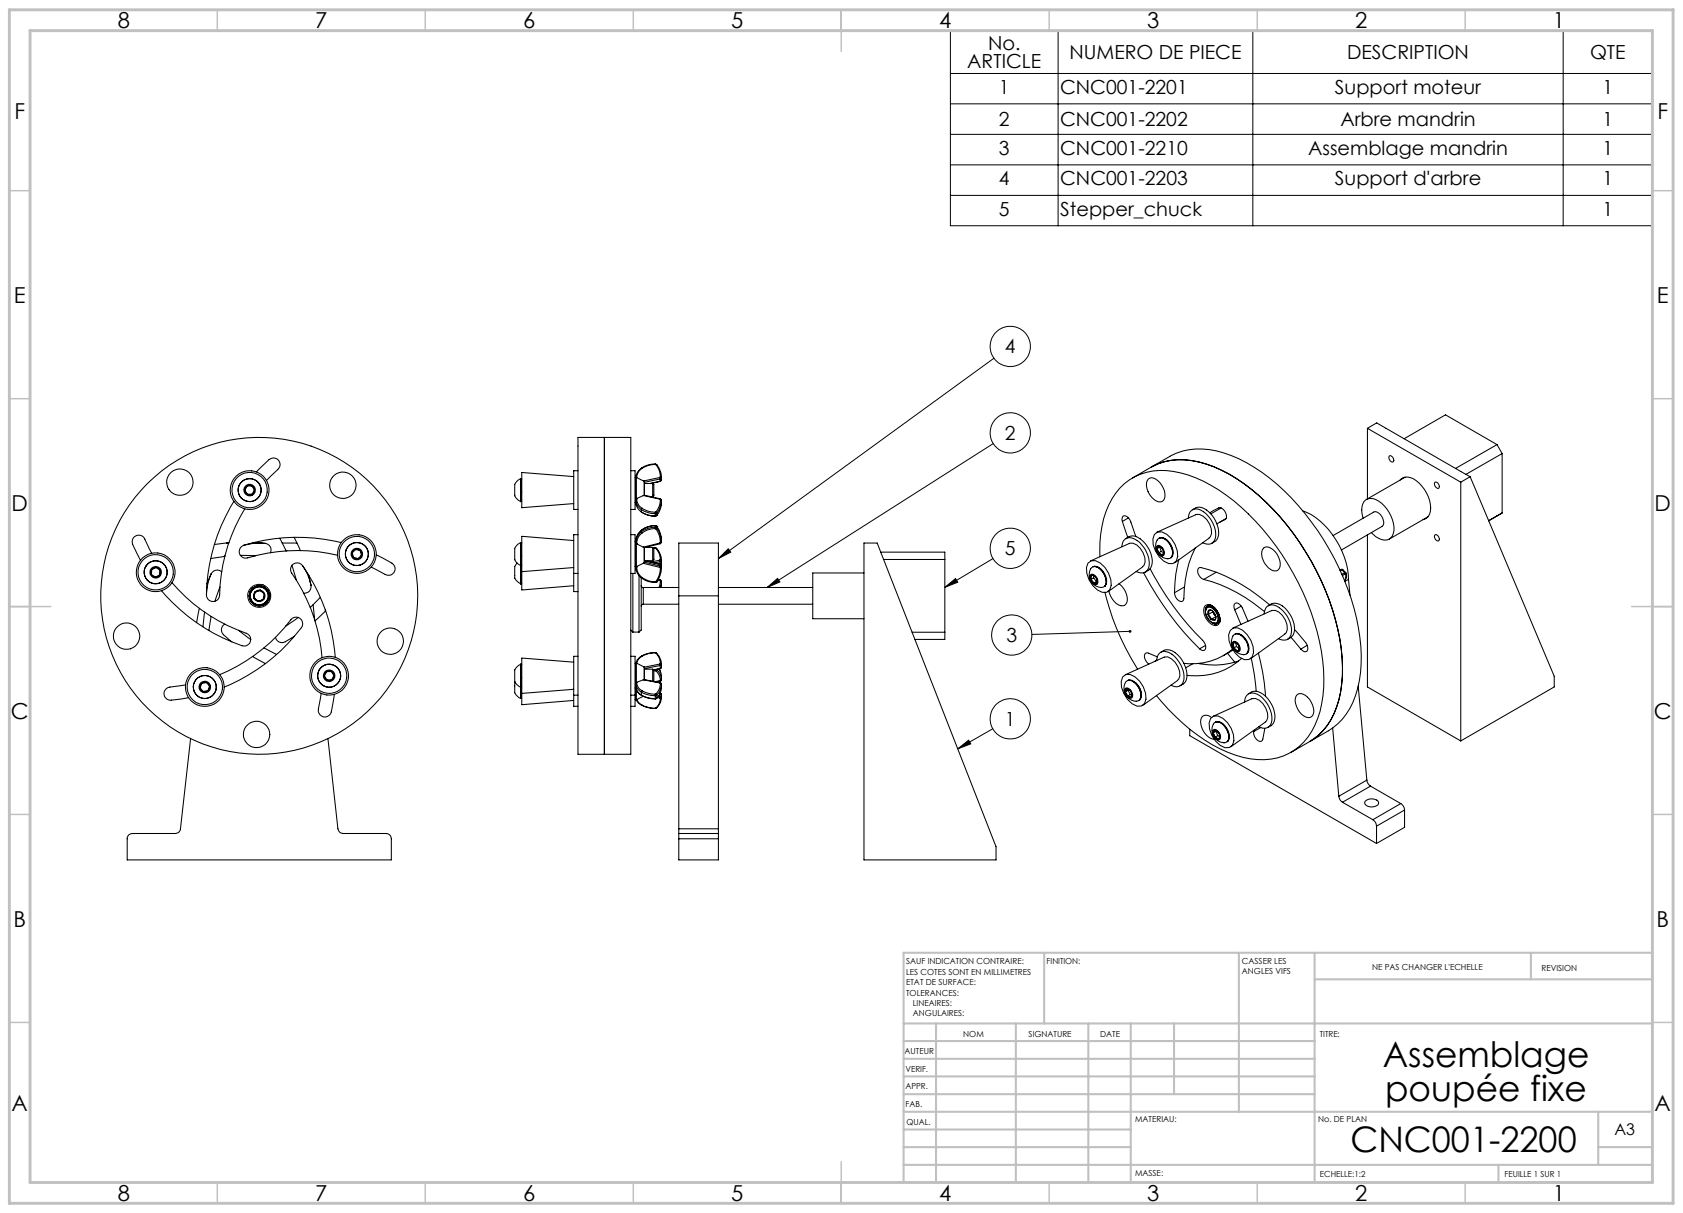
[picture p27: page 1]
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

No. ARTICLE | NUMERO DE PIECE | DESCRIPTION | QTE
1 | CNC001-2201 | Support moteur | 1
2 | CNC001-2202 | Arbre mandrin | 1
3 | CNC001-2210 | Assemblage mandrin | 1
4 | CNC001-2203 | Support d'arbre | 1
5 | Stepper_chuck | | 1

SAUF INDICATION CONTRAIRE:
LES COTES SONT EN MILLIMETRES
ETAT DE SURFACE:
TOLERANCES:
LINEAIRES:
ANGULAIRES:

NOM | SIGNATURE | DATE | | | | TITRE: Assemblage poupée fixe

AUTEUR
VERIF.
APPR.
FAB.
QUAL. | | | | MATERIAU: | No. DE PLAN CNC001-2200 | A3

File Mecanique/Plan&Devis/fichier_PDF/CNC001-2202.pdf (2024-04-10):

chanfreins 1x45°; FINITION:; CASSER LES; ANGLES VIFS; NE PAS CHANGER L'ECHELLE; REVISION; ECHELLE:1:1; FEUILLE 1 SUR 1

SAUF INDICATION CONTRAIRE:
LES COTES SONT EN MILLIMETRES
ETAT DE SURFACE:
TOLERANCES:
LINEAIRES:
ANGULAIRES:

NOM | SIGNATURE | DATE | | | | TITRE:

AUTEUR
VERIF.
APPR.
FAB.
QUAL. | | | | MATERIAU: | No. DE PLAN CNC001-2202 | A4

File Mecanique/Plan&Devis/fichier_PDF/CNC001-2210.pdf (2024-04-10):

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

No. ARTICLE | NUMERO DE PIECE | DESCRIPTION | QTE
1 | CNC001-2211 | Chuck cote moteur | 1
2 | CNC001-2212 | Chuck cote verre | 1
3 | 91306A716 | Button Head Hex Drive Screws | 5
4 | 93960A120 | Chrome-Plated Steel Washer | 10
5 | Bouchon caoutchouc | | 5
6 | 90866A029 | Zinc-Plated Steel Wing Nut | 5
7 | 90128A245 | Zinc-Plated Alloy Steel Socket Head Screw | 1

SAUF INDICATION CONTRAIRE:
LES COTES SONT EN MILLIMETRES
ETAT DE SURFACE:
TOLERANCES:
LINEAIRES:
ANGULAIRES:

NOM | SIGNATURE | DATE | | | | TITRE: Assemblage mandrin

AUTEUR
VERIF.
APPR.
FAB.
QUAL. | | | | MATERIAU: | No. DE PLAN CNC001-2210 | A3

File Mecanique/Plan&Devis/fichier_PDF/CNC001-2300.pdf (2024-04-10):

FINITION:; CASSER LES; ANGLES VIFS; NE PAS CHANGER L'ECHELLE; REVISION; ECHELLE:1:3; FEUILLE 1 SUR 1

No. ARTICLE | NUMERO DE PIECE | DESCRIPTION | QTE
1 | CNC001-2301 | Barre rail | 1
2 | CNC001-2302 | Charriot rail | 1
3 | CNC001-2303 | Préhenseur laser | 1
4 | CNC001-2304 | Laser | 1

SAUF INDICATION CONTRAIRE:
LES COTES SONT EN MILLIMETRES
ETAT DE SURFACE:
TOLERANCES:
LINEAIRES:
ANGULAIRES:

NOM | SIGNATURE | DATE | | | | TITRE: Assemblage Rail

AUTEUR
VERIF.
APPR.
FAB.
QUAL. | | | | MATERIAU: | No. DE PLAN CNC001-2300 | A3

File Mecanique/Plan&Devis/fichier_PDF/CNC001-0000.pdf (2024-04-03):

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

No. ARTICLE | NUMERO DE PIECE | DESCRIPTION | QTE
1 | CNC001-1000 | Assemblage bâti profilé | 1
2 | CNC001-2000 | Assemblage plaque | 1
3 | CNC001-2300 | Assemblage Rail | 1
5 | CNC001-1006 | Equerre coin | 16
6 | CNC001-1007 | Equerre T | 4

SAUF INDICATION CONTRAIRE:
LES COTES SONT EN MILLIMETRES
ETAT DE SURFACE:
TOLERANCES:
LINEAIRES:
ANGULAIRES:

NOM | SIGNATURE | DATE | | | | TITRE:

AUTEUR
VERIF.
APPR.
FAB.
QUAL. | | | | MATERIAU: | No. DE PLAN CNC001-0000 | A3


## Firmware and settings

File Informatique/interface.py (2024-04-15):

# Interface Management
from Windows.Graphicus03_Main import Ui_Graphicus03
from PySide2.QtWidgets import QApplication, QMainWindow, QGraphicsScene, QGraphicsRectItem, QGraphicsPolygonItem
from PySide2.QtCore import QPointF, Qt, Signal, QThread, QObject
from PySide2.QtGui import QPolygonF, QPen
# File Management with explorer
import tkinter
from tkinter import filedialog
# Read data from svg file
from xml.dom import minidom
# from svgpathtools import parse_path
from svgpath2mpl import parse_path
from math import sqrt
from queue import Queue
# test output
import json
from time import sleep

class Interface(Ui_Graphicus03, QMainWindow):
    def __init__(self, queueOut: Queue, queueIn: Queue):
        """Creer l'interface pour Graphicus-03

        Args:
            queueOut (Queue): Queue sortant les données de l'interface
            queueIn (Queue): Queue aillant les données entrante à l'interface
        """
        super(Interface, self).__init__()
        self.setupUi(self)
        self.scene = QGraphicsScene(0, 0, 200, 140)
        self.screen_info = None
        self.modifySetup()
        self.selected_file = "None"
        self.polygonItems = []
        self.queueIn = queueIn
        self.queueOut = queueOut
        self.setupConnection()

    def setupConnection(self):
        """Creer les connections pour les boutons de l'interface
        """
        self.PB_selectFile.pressed.connect(self.fileSelection)
        self.PB_launch.pressed.connect(self.startExecution)

    def modifySetup(self):
        """Modifie le setup fait par QtDesing
        """
        self.GV_logo.setScene(self.scene)
        self.CB_material.addItems(["Plastique", "Vitre", "Métal"])
        for CB_unit in [self.CB_unit_radius, self.CB_unit_Largeur, self.CB_unit_Hauteur]:
            CB_unit.addItems(["cm", "mm", "po"])
        for DSB_item in [self.DSB_Hauteur, self.DSB_Largeur, self.DSB_radius]:
            DSB_item.setValue(5)

    def fileSelection(self):  
        """Ouvre l'exploreur de fichier pour selectionner un SVG
        """
        tkinter.Tk().withdraw()
        selected_file_temp = filedialog.askopenfile(filetypes=[("vector files", ["*.svg"]), ("all files", "*")])
        if selected_file_temp != None:
            self.selected_file = selected_file_temp
            self.LE_csvFile.setText(self.selected_file.name)
            self.modifyImageViewer()

    def modifyImageViewer(self):
        """Modifie l'image du logo sur le graphique view avec l'image provenant du fichier SVG
        """
        self.scene.clear()
        # get the svg information from file
        doc = minidom.parse(self.selected_file.name)
        path_strings = [path.getAttribute('d') for path
                        in doc.getElementsByTagName('path')]
        width = [svg.getAttribute('width') for svg in doc.getElementsByTagName("svg")]
        height = [svg.getAttribute('height') for svg in doc.getElementsByTagName("svg")]
        doc.unlink()

        # create map of point from svg path
        mpl_path = parse_path(str(path_strings))
        coords = mpl_path.to_polygons()
        self.scene = QGraphicsScene(-10, -10, self.GV_logo.width(), self.GV_logo.height())
        self.GV_logo.setScene(self.scene)
        self.polygonItems = []
        closest_point = []
        fartest_point = []
        for tableau in coords:
            new_polygon = QPolygonF()
            for points in tableau:
                new_point = QPointF(points[0], points[1])
                new_polygon.append(new_point)
            new_item = QGraphicsPolygonItem()
            new_item.setPolygon(new_polygon)
            self.polygonItems.append(new_item)
            self.scene.addItem(new_item)
            # calcul de combien il faut décaller les items pour les ramener à l'origine (0, 0)
            distance = self.get_distance_from_origine(new_item)
            if closest_point == []:
                closest_point = distance
            else:
                if closest_point[1] > distance[1]:
                    closest_point[1] = distance[1]
                if closest_point[2] > distance[2]:
                    closest_point[2] = distance[2]
            if fartest_point == []:
                fartest_point = distance
            else:
                if fartest_point[3] < distance[3]:
                    fartest_point[3] = distance[3]
                if fartest_point[4] < distance[4]:
                    fartest_point[4] = distance[4]
                    
        scale_to_img_x = self.GV_logo.width()/(fartest_point[3]-closest_point[1])
        scale_to_img_y = self.GV_logo.height()/(fartest_point[4]-closest_point[2])
        scale = scale_to_img_x/2
        if scale_to_img_y < scale_to_img_x:
            scale = scale_to_img_y/2
        self.scale_pic = scale
        # déplace tous les items vers l'origine avec le décalage calculé précédement        
        pen_item = QPen(
            Qt.black,
            0.5/scale,
            Qt.SolidLine,
            Qt.RoundCap,
            Qt.RoundJoin
            )
        for item_ in self.polygonItems:
            item_.setScale(scale)
            item_.setPos(item_.pos() - QPointF(closest_point[1]*scale, closest_point[2]*scale)) 
            item_.setPen(pen_item)
        self.scene.setSceneRect(0, 0, fartest_point[3]*scale-closest_point[1]*scale, fartest_point[4]*scale-closest_point[2]*scale)
        self.x_offset = closest_point[0]
        self.y_offset = closest_point[1]
        

    def get_distance_from_origine(self, graphic_item: QGraphicsPolygonItem):
        """Retourne la distance entre le entre l'origine (0, 0) et la position d'un QGraphicsItem

        Args:
            graphic_item (QGraphicsPolygonItem): Un item du QGraphicView

        Returns:
            [float, int, int, int, int] : [distance entre (0, 0) et origine du rectangle, x_origine item, y_origine item, x_final item, y_final item]
        """
        b_rect = graphic_item.boundingRect()
        distance = sqrt(b_rect.x()**2 + b_rect.y()**2)
        return [distance, b_rect.x(), b_rect.y(), b_rect.x()+b_rect.width(), b_rect.y()+b_rect.height()]

    def startExecution(self):
        """lance le signal dans la Queue pour débuter la gravure et initilise la reception des positions pour graver et desactive les widgets de l'interface
        """
        # disable the hole screen
        all_widgets = [self.CB_material, self.CB_unit_Hauteur, self.CB_unit_Largeur, self.CB_unit_radius,
                       self.DSB_Hauteur, self.DSB_Largeur, self.DSB_radius, self.LE_csvFile, self.PB_launch, 
                       self.PB_selectFile]
        for wid in all_widgets:
            wid.setDisabled(True)
            wid.update()
       
        self.thread = QThread()
        self.worker = worker(self.queueOut, self)
        self.worker.moveToThread(self.thread)
        # connecter les signaux entre le worker et la thread associé
        self.thread.started.connect(self.worker.run_)
        self.worker.finished.connect(self.thread.quit)
        self.worker.finished.connect(self.worker.deleteLater)
        self.thread.finished.connect(self.thread.deleteLater)
        # start the thread
        self.thread.start()

    @staticmethod
    def getMesureInmm(value, unit):
        """Converti les valeur entree en mm

        Args:
            value (float): valeur numerique a convertir
            unit (string): mm, cm, ou po

        Returns:
            _type_: _description_
        """
        if unit == "mm":
            return value
        elif unit == "cm":
            return value*10
        elif unit == "po":
            return value*25.4
        else:
            return 0

    
class worker(QObject):
    finished = Signal()
    _progress = Signal(tuple)

    def __init__(self, queueOut:Queue, parent):
        """Worker calculant le dictionnaire de controle laser et l'envoie dans la queueOut

        Args:
            queueOut (Queue): Queue sortant de l'interface
            parent (Interface): Interface utilisant le worker
        """
        super().__init__()
        self.queueOut = queueOut
        self.parent = parent

    def run_(self):
        """Execution du worker
        """
        ls_laser = {}
        max_x = 0
        max_y = 0
        min_x = []
        min_y = []
        width  = self.parent.getMesureInmm(self.parent.DSB_Largeur.value(), self.parent.CB_unit_Largeur.currentText())
        height = self.parent.getMesureInmm(self.parent.DSB_Hauteur.value(), self.parent.CB_unit_Hauteur.currentText())
        radius = self.parent.getMesureInmm(self.parent.DSB_radius.value() , self.parent.CB_unit_radius.currentText())
        for item in self.parent.scene.items():
            bounding_rec = item.boundingRect()  
            delta = 10          

            top     = (bounding_rec.topLeft().x() -delta) * self.parent.scale_pic
            left    = (bounding_rec.topLeft().y() -delta) * self.parent.scale_pic
            bot     = (bounding_rec.bottomRight().x() +delta) * self.parent.scale_pic
            right   = (bounding_rec.bottomRight().y() +delta) * self.parent.scale_pic
            min_x.append(top - self.parent.x_offset)
            min_y.append(left - self.parent.y_offset)
            precision:int = 1
            for y in range(int(right - left)*precision):
                yy = int(y + left - self.parent.y_offset) 
                if not ls_laser.__contains__(yy):
                    ls_laser[yy] = {}
                for x in range(int(bot - top)*precision):
                    xx = int(x + top - self.parent.x_offset)
                    if not ls_laser[yy].__contains__(xx):
                        ls_laser[yy][xx] = False
                    if item.contains(QPointF((x + top)/self.parent.scale_pic, (y + left)/self.parent.scale_pic)):
                        ls_laser[yy][xx] = not ls_laser[yy][xx]
            if xx>max_x:
                max_x = xx
            if yy>max_y:
                max_y = yy
      
        myKeys = list(ls_laser.keys())
        myKeys.sort()
        myValues = list(list(ls_laser.values())[0].keys())
        myValues.sort()
        min_value = min(min_x)
        min_key = min(min_y)
        new_ls_laser = {}
        length_x = max_x - min_value
        length_y = max_y - min_key
        self.parent.dim_zone = (length_x, length_y)
        for key in ls_laser.keys():
            value = ls_laser[key]
            new_value = {}
            for value_key in value.keys():
                new_value[width*(value_key - min_value - delta/2)/length_x] = value[value_key]
            new_ls_laser[height*(int(key) - min_key - delta/2)/length_y] = new_value
        with open("sortie_bounding_rect_met.json", 'w') as f:
            json.dump(new_ls_laser, f, indent=4)
        self.parent.ls_laser = new_ls_laser
        sleep(2)
        self.parent.queueOut.put(["debut", width, height, radius, self.parent.ls_laser])
        
        sleep(5)
        self.finished.emit()

def initWindow(queueOut, queueIn):
    """Lance la fenetre Interface

    Args:
        queueOut (Queue): Queue sortant de l'interface
        queueIn (Queue): Queue entrant dans l'interface
    """
    app = QApplication([])
    win = Interface(queueOut, queueIn)
    win.show()
    # PySide_dark_theme.toggleDarkTheme(app, PySide_dark_theme.darkTheme())
    app.exec_()

if __name__ == "__main__":
    # lance le protocole de test de gravure 
    initWindow(None, None)

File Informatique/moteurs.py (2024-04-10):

from queue import Queue
import RPi.GPIO as GPIO
import time
from math import pi

class Moteurs:
    def __init__(self, queue_in : Queue, queue_out : Queue):
        """Initialisation de l'objet moteur, initialisation des entrées/sorties du Raspberry Pi,
        appel des fonctions de calibration de la machine.

        Args:
            queue_in (Queue): File synchronisé pour les entrées provenant de l'interface
            queue_out (Queue): File synchronisé pour les sorties provenant des moteurs
        """
        super(Moteurs, self).__init__()

        self.enable_pin1, self.coil_A1, self.coil_B1, self.coil_C1, self.coil_D1 = 1,23,20,22,12 
        self.enable_pin2, self.coil_A2, self.coil_B2, self.coil_C2, self.coil_D2 = 1,4,13,27,21 
        self.enable_pin3, self.coil_A3, self.coil_B3, self.coil_C3, self.coil_D3 = 1,17,9,18,10 
        self.LASER_pin = 16

        GPIO.setwarnings(False)
        GPIO.setmode(GPIO.BCM)
        GPIO.setup((self.enable_pin1, self.coil_A1, self.coil_B1, self.coil_C1, self.coil_D1), GPIO.OUT, initial=GPIO.LOW)
        GPIO.setup((self.enable_pin2, self.coil_A2, self.coil_B2, self.coil_C2, self.coil_D2), GPIO.OUT, initial=GPIO.LOW)
        GPIO.setup((self.enable_pin3, self.coil_A3, self.coil_B3, self.coil_C3, self.coil_D3), GPIO.OUT, initial=GPIO.LOW)
        GPIO.setup(self.LASER_pin, GPIO.OUT, initial=GPIO.LOW)
        self.limit_switch_pins = [24,25,5,6]  
        GPIO.setup(self.limit_switch_pins, GPIO.IN, pull_up_down=GPIO.PUD_UP)

        self.stepper_position_queue = Queue()
        self.stepper_angle_queue = Queue()
        self.queue_out = queue_out
        self.queue_in = queue_in
        self.stepper_position = [0,0,0]
        self.stepper_angle = 0
        self.angle_rotation = 1.8

        self.queue_button_start = False
        self.queue_gravx = 0
        self.queue_gravy = 0
        self.queue_radius = 0
        self.laser_control = {}
        self.no_limit3 = 0
        self.num_step1 = 0
        self.num_step2 = 0
        self.num_step3 = 0

        self.enable_stepper_motor(1)
        self.enable_stepper_motor(2)
        self.enable_stepper_motor(3)
        self.laser_go_to_home()
        self.move_board_down()
        self.move_stepper_motor_forward(3, 4, 350)

    def is_limit_switch_triggered(self, switch_id):
        """Fonction permettant la vérification de l'état d'un capteur de fin de course.
        Une moyenne sur 10 valeurs est effectué afin d'éviter les fausses valeurs.

        Args:
            switch_id (int): Identifiant de l'interrupteur de fin de course (1-4)

        Returns:
            bool: True si le capteur de fin est activé, False sinon
        """
        readings = []
        for _ in range (10):
            readings.append(GPIO.input(self.limit_switch_pins[switch_id-1]))
        return all(readings)
    
    def enable_stepper_motor(self, motor_id):
        """Fonction permettant l'activation du moteur pas-à-pas spécifié

        Args:
            motor_id (int): Identifiant du moteur pas-à-pas (1-3)
        """
        enable_pin = self.get_enable_pin(motor_id)
        GPIO.output(enable_pin, GPIO.HIGH)

    def disable_stepper_motor(self, motor_id):
        """Fonction permettant la désactivation du moteur pas-à-pas spécifié

        Args:
            motor_id (int): Identifiant du moteur pas-à-pas (1-3)
        """
        enable_pin = self.get_enable_pin(motor_id)
        GPIO.output(enable_pin, GPIO.LOW)

    def get_enable_pin(self, motor_id):
        """Fonction permettant la récupération du numéro de broche de contrôle pour les moteurs pas-à-pas

        Args:
            motor_id (int): Identifiant du moteur pas-à-pas (1-3)

        Returns:
            int: Numéro de broche de contrôle du moteur spécifié
        """
        if motor_id == 1:
            return self.enable_pin1
        elif motor_id == 2:
            return self.enable_pin2
        elif motor_id == 3:
            return self.enable_pin3

    def stop_motors(self):
        """Fonction permettant la désactivation des moteurs en désactivant toutes les bobines
        """
        GPIO.output(self.coil_A1, GPIO.LOW)
        GPIO.output(self.coil_B1, GPIO.LOW)
        GPIO.output(self.coil_C1, GPIO.LOW)
        GPIO.output(self.coil_D1, GPIO.LOW)

        GPIO.output(self.coil_A2, GPIO.LOW)
        GPIO.output(self.coil_B2, GPIO.LOW)
        GPIO.output(self.coil_C2, GPIO.LOW)
        GPIO.output(self.coil_D2, GPIO.LOW)

        GPIO.output(self.coil_A3, GPIO.LOW)
        GPIO.output(self.coil_B3, GPIO.LOW)
        GPIO.output(self.coil_C3, GPIO.LOW)
        GPIO.output(self.coil_D3, GPIO.LOW)

    def move_stepper_motor_forward(self, motor_id, steps, speed):
        """Fonction permettant de faire avancer le moteur pas-à-pas spécifié d'un certain nombre de pas à une vitesse donnée

        Args:
            motor_id (int): Identifiant du moteur pas-à-pas (1-3)
            steps (int): Nombre de pas à effectuer
            speed (int): Vitesse de déplacement du moteur
        """
        if speed > 525:
            speed = 525

        if motor_id == 1:
            limit_switch_pin2 = 2
        elif motor_id == 2:
            limit_switch_pin2 = 3
        elif motor_id == 3:
            limit_switch_pin2 = self.no_limit3
        
        coil_sequence = [(1, 0, 1, 0), (0, 1, 1, 0), (0, 1, 0, 1), (1, 0, 0, 1)]
        delay_ = 1.0 / speed
        step_count = 0
        start_time = time.time() 
        
        while step_count < steps:    
            elapsed_time = time.time() - start_time
            
            if elapsed_time >= delay_:
                if motor_id == 1:
                    self.num_step1 +=1
                    if self.num_step1>3:
                        self.num_step1 = 0
                    coils = coil_sequence[self.num_step1]
                if motor_id == 2:
                    self.num_step2 +=1
                    if self.num_step2>3:
                        self.num_step2 = 0
                    coils = coil_sequence[self.num_step2]
                if motor_id == 3:
                    self.num_step3 +=1
                    if self.num_step3>3:
                        self.num_step3 = 0
                    coils = coil_sequence[self.num_step3]
                for coil_pin, coil_state in zip(self.get_coil_pins(motor_id), coils):
                    GPIO.output(coil_pin, GPIO.HIGH if coil_state else GPIO.LOW)

                start_time = time.time() 
                step_count += 1
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

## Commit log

2024-01-17 Debut de la classe moteur et premiere definition des fonctions
2024-01-28 Fonctions principales completes, implementation de la fonction gravure manquante.
2024-01-28 Add files via upload
    Principales fonctions completes, implementation de la fonction gravure manquante
2024-01-30 Squelette de base - 20240130
2024-02-06 Added check for move board function - added read_values function
2024-02-07 Ajout de Qthread, de progressBar et de ComboBox pour hauteur et largeur
2024-02-10 Bug fixes, distance bug still present
    [class_moteurs.py]
2024-03-13 interface qui resize l'image dans le QGraphicViews
    [Stocks.csv, data_x_x2_x3.csv, msft.csv]
2024-03-13 Mesure envoyée de l'interface vers les moteur en millimètre
2024-03-13 stop readin queue of motor
2024-03-13 ignore limit switch
2024-03-13 setup thread communication between motor and interface
2024-03-13 interface and motors no error
    [interface.py]
2024-03-13 added prints for debugging
2024-03-13 RB call of motors with queue
2024-03-13 RP Motor sequence travail en cour
2024-03-13 RP motor change suite
2024-03-13 RP everything is working except the progress bar and the "worker" thread in the interface
2024-03-13 interface thread without interacting with the GUI
2024-03-20 test on assembly
2024-03-20 print ls
2024-03-20 added no safe move for homing
2024-03-20 update motor_id
2024-03-20 board test
2024-03-20 change ls board
2024-03-20 test board
2024-03-20 final implementation on assembly
2024-03-20 Final implementation of moteurs on assembly
2024-03-20 GPIO de gestion de laser
2024-03-20 Ajout de la detection par item ls_laser
2024-03-20 ajout du test laser
2024-03-20 manque ajout de mutexe
2024-03-28 removed thread motor2
2024-03-28 changed steps for laser
2024-03-28 changed delay for laser
2024-03-28 changed steps motor3 for grav
2024-03-28 renommer la classe moteur
2024-04-03 new detection laser
2024-04-03 Add files via upload
    Ajout des STL
    [BoiteElectrique100.stl, BoiteElectrique101.stl, BoiteElectrique103.stl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]
2024-04-03 ajout de icecream pour le debuggage
2024-04-03 controle du laser par la classe moteur
2024-04-03 RP - Laser fonctionnel
2024-04-03 test de moteur rotation verre
2024-04-03 ajout de diagonale.svg
2024-04-03 added step memory for all motors
2024-04-10 changed speed for motor3
2024-04-10 26-18 pin motor3
2024-04-11 Deplacement vers informatique
    [Stocks.csv, data_x_x2_x3.csv, msft.csv]
2024-04-11 Deplacement de SVG vers Informatique
2024-04-11 Deplacement de Windows vers Informatique
2024-04-11 Deplacement de __pycache__ vers Informatique
2024-04-11 Deplacement de modules vers Informatique
2024-04-11 Deplacement de test_validation vers Informatique
2024-04-11 Deplacement des fichiers non classé dans Informatique
2024-04-14 Pieces et assemblage SW
2024-04-15 description ajouter dans la classe Interface
